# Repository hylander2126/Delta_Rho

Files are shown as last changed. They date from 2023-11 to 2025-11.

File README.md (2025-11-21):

# Delta Rho Robot
3D models, firmware, and MATLAB control scripts for the Delta-Rho swarm robotic platform at WPI's Soft Robotics Laboratory. Contact Cagdas Onal (cdonal@wpi.edu) or Steven Hyland (smhyland@wpi.edu) for more information.

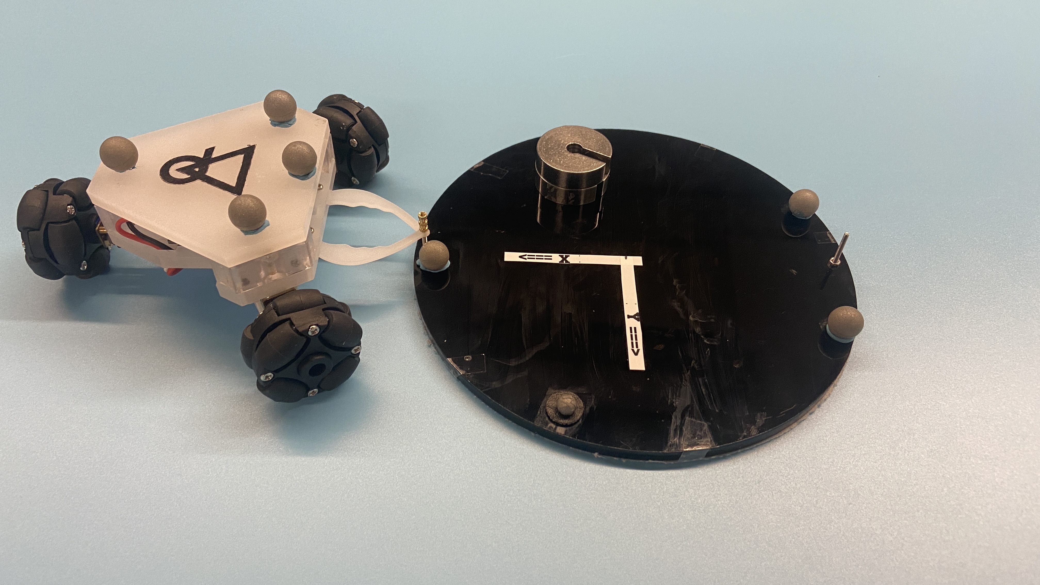
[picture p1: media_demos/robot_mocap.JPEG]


### Hardware:
#### PCB
The robot currently uses a custom PCB housing a ATMega1284p chip. More details along with a schematic can be found in the hardware/controller_board folder. It can be powered via 7.4V LiPo battery, make sure not to flip + and -

#### CAD
Currently, the robot is designed in SolidWorks, with most of the chassis and body 3D printed. Other necessary and optional components can be found in the hardware/CAD folder.

### Firmware:
Flashing firmware to the robot is performed with a standard AVRISP MKII programmer over ISP interface. Connect the programmer to the robot following following the correct wiring:
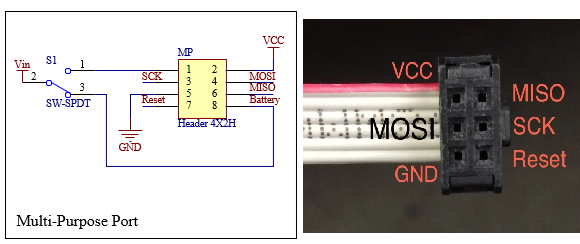
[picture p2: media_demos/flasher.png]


Use Microchip Studio and open the 'Delta_Rho_controller.atsln' solution file. Code is written in C, and can be flashed to the robot using the 'start debugging' button or pressing 'f5'. Currently, the firmware allows for onboard computation, code execution, etc. but can also be moved offboard to MATLAB (controller code provided in 'control_single_robot' folder). 

NOTE: the ROBOT ID at the top of the robot code is critical for communicating and differentiating between robots when handling a multi-robot swarm. If you are worried about interference between other robots, set these IDs to some unique integer (1 to 255). 

MATLAB Communication is performed through two Xbee RF modules, one 'server' attached to the PC via USB adapter, and one 'client' attached to the header on the robot board.  The demo script should get you started with sending velocity commands to the robot. See the 'utilities' folder for more functions.


#### Communication:
XBee modules need to be flashed to operate on the same bandwidth and to determine the 'server' and 'client' modules, respectively. This setup only needs to be performed once on new XBee modules. 

(TODO: Add programming instructions)

### Simulation:
Currently, all the simulation is performed in MATLAB. Other simulation software is in progress.

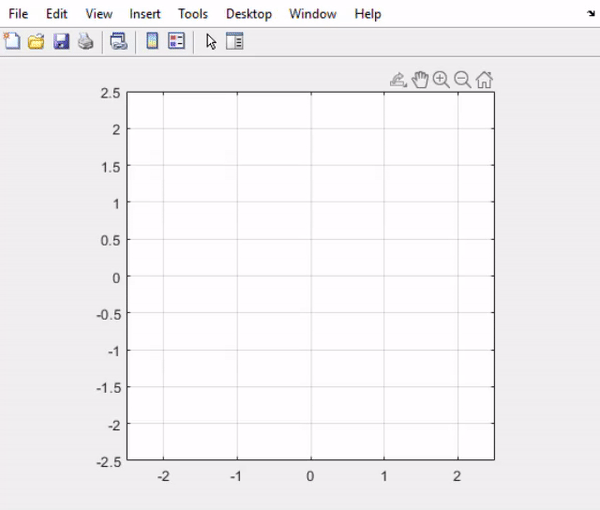
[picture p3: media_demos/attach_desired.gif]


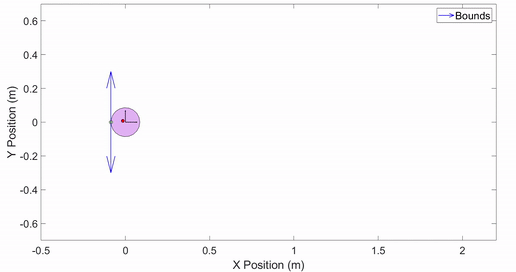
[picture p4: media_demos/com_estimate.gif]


---

Reach out to Steven Hyland at smhyland@wpi.edu for further questions or concerns.

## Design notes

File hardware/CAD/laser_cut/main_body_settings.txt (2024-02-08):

Cover spring slots with tape
2-3 raster passes at 15% speed 25% power

3 vector cuts at 15% speed 60% power

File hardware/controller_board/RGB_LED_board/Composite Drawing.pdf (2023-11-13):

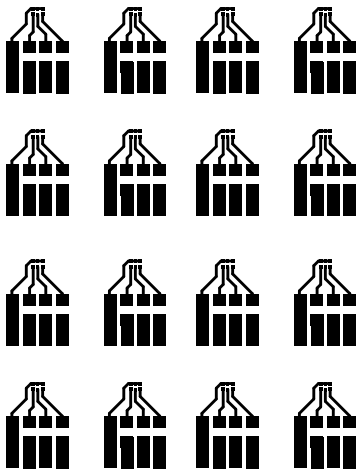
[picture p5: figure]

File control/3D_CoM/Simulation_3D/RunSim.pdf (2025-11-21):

## Full 3D Simulation of CoM Estimation Strategy

clc; clear; close all;
addpath("Utilities\");

% First set the problem and object parameters (FOR NOW A RECTANGULAR BOX)
mass | = 1;
fric | = 0.5;
width | = 2;
height = 4;
origin = [0; 0; 0]; % ORIGIN (for simplicity, this is at tipping edge on smallest y (into page) vertex)
com | = [-width/2; width/2; height/2]; % com defined from origin
hf | = 3; | % Height above the table where f applied
Pf | = [-width; 1; hf]; % point of external force applied
Fp | = [1; 0; 0]; % magnitude of linear force applied
viewf | = [0 -1 0]; % Front view (-y towards camera)
viewt | = [0 0 1]; % Top view (z towards camera)

body = body('mass',mass, 'mu',fric, 'com',com, 'width',width, ... 'height',height, 'Pf',Pf, 'Fp',Fp, 'origin',[-width;0;0]);

% Now visualize the object

% 3D view
body.plot(gca); hold off; figure;

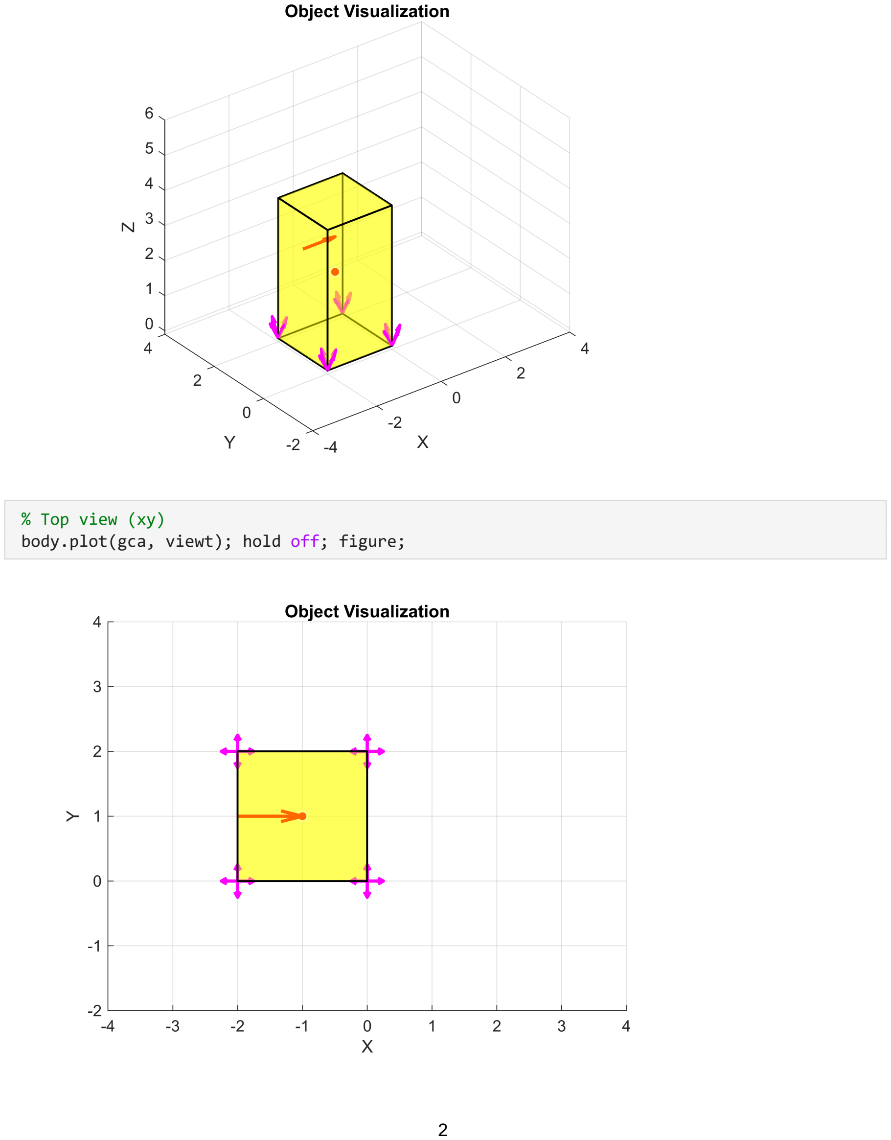
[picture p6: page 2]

% Top view (xy)
body.plot(gca, viewt); hold off; figure;

% Front view (xz)
body.plot(gca, viewf); hold off; figure;

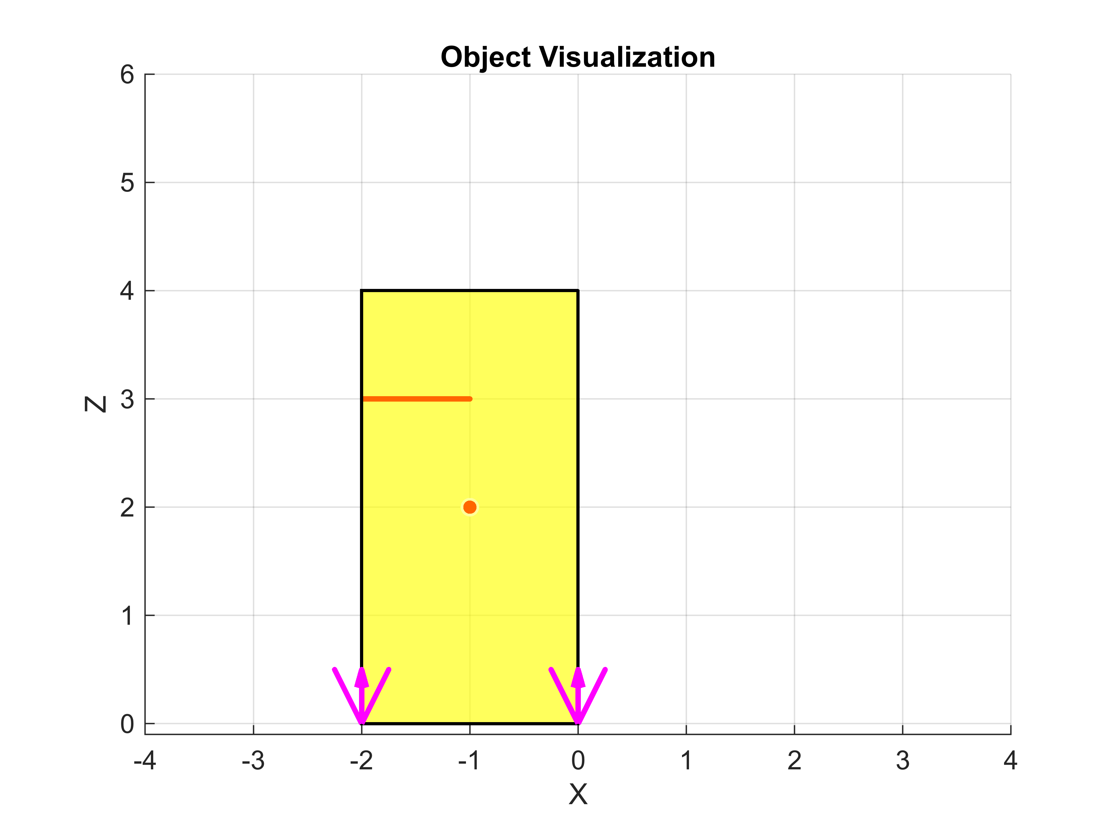
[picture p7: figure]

### First, scalar analysis of the SLIDING/TIPPING condition

% Scalar being the basic sliding/tipping thresholds

syms mu m g r_w h_c d positive
syms F_p h_f real

% Incipient SLIDING is when F(push) >= f(fric). recall that {ft <= mu*f(normal)}. x-axis equilibrium.
slide_F = solve( F_p == mu*m*g, F_p );

% Incipient TIPPING is when M(push) > M(gravity). recall that {M = f*r}. y-axis moment equilibrium.
% (also recall at incipient tip, norm and fric generate no moment since they occur @ tipping point
tip_F = solve( F_p*h_f == m*g*r_w, F_p );

% tip_cond_F = solve(subs(tip_eqn, [m g r_w h_f], [mass 9.8 -body.com(1) hf]), F_p) % r_w from com to tip edge
% should probably generalize ^this^ to check for the furthest point from the push side, but not for now slide_val = double( subs(slide_F, [mu,m,g], [fric,mass,9.8]) );
tip_val | = double( subs(tip_F, | [m,g,r_w,h_f], [mass,9.8,abs(body.com(1)),hf]) );

% Print Conditionals
cond = 'SLIDING and TIPPING';
if isAlways(slide_val < tip_val); cond = char('SLIDING'); end
if isAlways(tip_val < slide_val); cond = char('TIPPING'); end
fprintf('F required for sliding: %.3f and tipping: %.3f', slide_val, tip_val)

F required for sliding: 4.900 and tipping: 3.267
fprintf('\n%s will occur because its the smaller of the two by: %.3f.\n', cond, abs(round(slide_val - tip_val, 3)))

TIPPING will occur because its the smaller of the two by: 1.633.

% For fun, find height where sliding and tipping occurs simultaneously, given current object geometry
ts_eqn = solve(m*g*r_w/(h_f) == mu*m*g, h_f);
ts_val = double( subs(ts_eqn, [r_w mu], [-com(1) fric]) );
fprintf('h_f required for current geometry and friction: %.3f', ts_val)

h_f required for current geometry and friction: 2.000

### Next, scalar analysis of TOPPLING condition

% A finger located at Pf (relative to object frame) continually pushes with force Fp until object comes to
% unstable equilibrium (ZMP: zero moment point). At any time t during motion, static equilibrium is present

% Assume TIPPING condition is active i.e. F(t=0) = F_tip
F = tip_val;
angle_step = -0.1; % degrees. 'step' for each object/plotting update. Can be arbitrarily small.
flist = [];
topple_i = 0;

% Lets 'simulate' bringing object to toppling threshold. No physics, just visual + geometry analysis.
while F > 0
% The force required for equilibrium drops bc rw drops AND hf increases
rw_i = -body.com(1); | % x-distance from CoM to tip edge
hf_i = body.Pf(3); | % z-distance (height) of push from tip edge
% Moment equation at this time
F = (9.8*mass*rw_i)/hf_i;

topple_i = topple_i + 1;
flist = [flist; F]; % (this is the force required to maintain equilibrium at current time)

T = [R3(angle_step, [0;-1;0],'deg') [0;0;0]; 0 0 0 1];
body.move(T)
% body.plot(gca, viewf) % Uncomment to plot in the loop (CAUTION: THIS MAY CRASH MATLAB)
end

% Visualize the object and the Force graph
body.plot(gca, viewf);

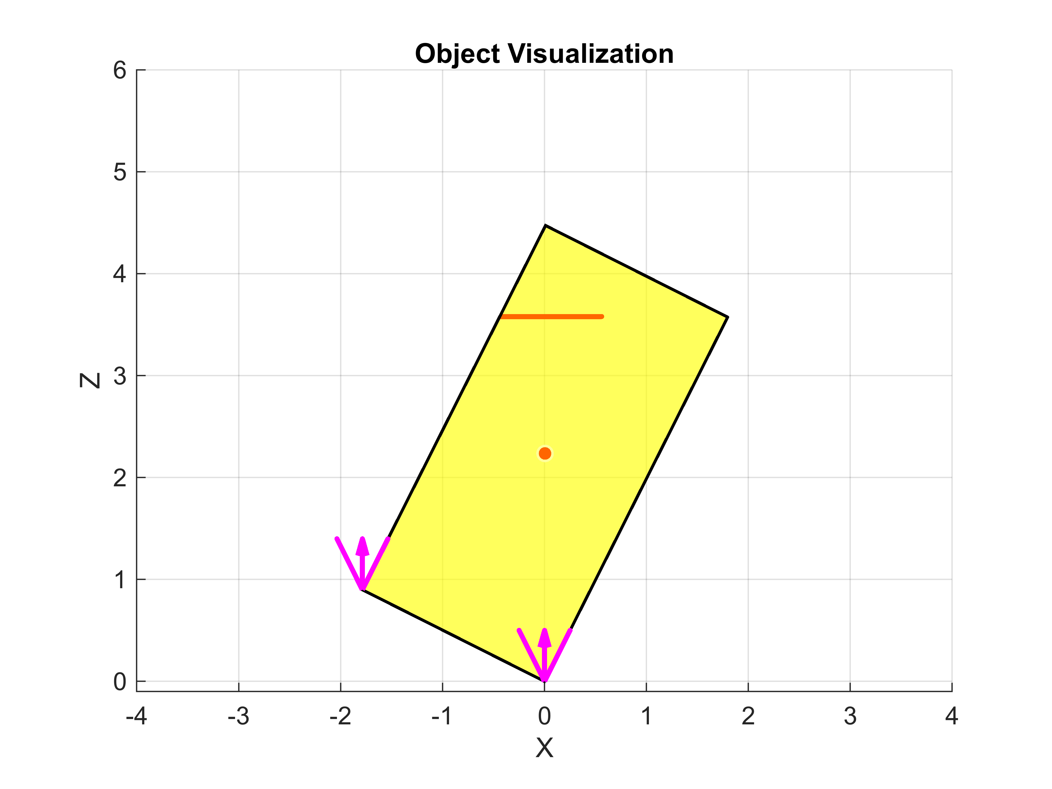
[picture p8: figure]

figure; plot(flist); hold on; xlim([0, topple_i]); ylim([-0.5 tip_val+0.5]); yline(0,'--r');
title('Force Required to Maintain Equilibrium'); hold off;

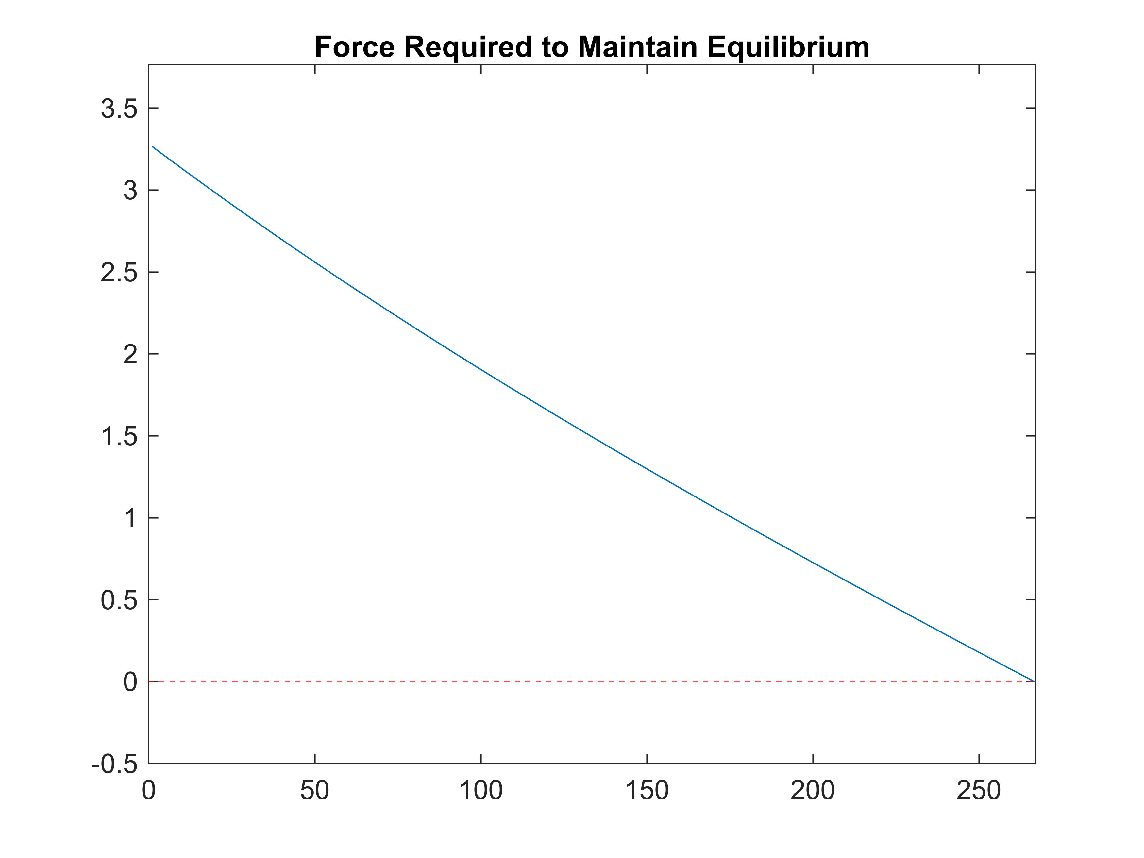
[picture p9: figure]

% Now we know the final angle of the payload at which toppling occurs. topple_final_angle = angle_step*topple_i;
fprintf('\nToppling occurs at object angle %.2f deg.', topple_final_angle)

Toppling occurs at object angle -26.70 deg.

% Let's reset the object for the next section reset_angle = -topple_final_angle;
T = [R3(reset_angle, [0;-1;0],'deg') [0;0;0]; 0 0 0 1];
body.move(T);

### Now, let's try approximating the force curve with a small push

angle_step = -0.1; % again, arbitrary. akin to time step.
final_angle = -5; % degrees. 'final' angle - bring object to this angle and no further
topple_angles = [];
flist_approx = [];

start_angle = 0;

for j = 0 : angle_step : final_angle
% The force required for equilibrium drops because rw drops AND hf increases

rw_i = -(body.com(1));
hf_i = body.Pf(3);
% Moment equation at this time
F_approx = (9.8*mass*rw_i)/hf_i;

topple_angles = [topple_angles; j];
flist_approx = [flist_approx; F_approx]; % (this is the force required to maintain equilibrium at current time)

T = [R3(j - start_angle, [0;-1;0],'deg') [0;0;0]; 0 0 0 1];
body.move(T);
% body.plot(gca, viewf) % Uncomment to plot in the loop (CAUTION: THIS MAY CRASH MATLAB)
start_angle = j;
end

% For visualization, make topple angles positive topple_angles_mag = abs(topple_angles);

% Visualize the object and the Force graph close all;
body.plot(gca, viewf); hold off;

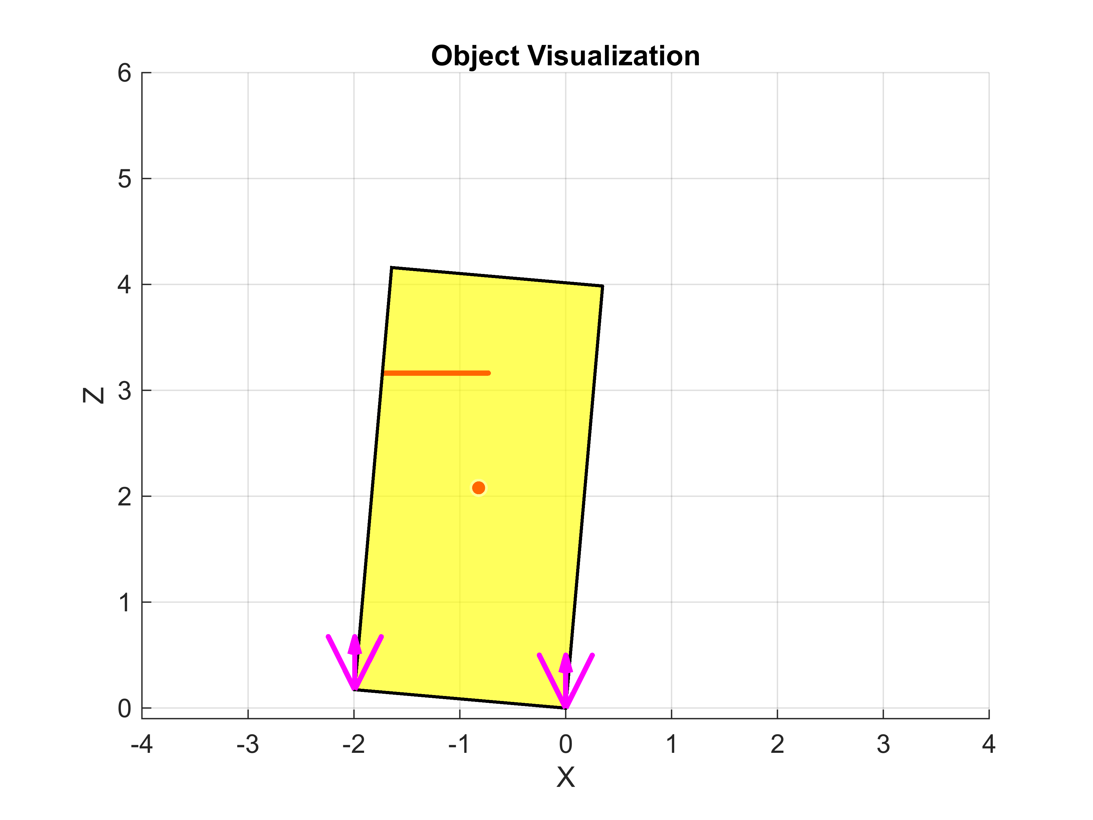
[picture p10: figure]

figure; plot(topple_angles_mag, flist_approx); yline(0,'--r'); title('Force Required to Maintain Equilibrium'); hold on;

% Now let's approximate the force curve given the data subset
n = 1; % use 5th order for decent approximation
p = polyfit(topple_angles_mag, flist_approx, n); % Fit a polynomial approximation r = roots(p);
topple_angle_approx = r( imag(r)==0 ); % Save only the real roots

% Visualize the approximation
xx = linspace(abs(final_angle), topple_angle_approx, 20);
yy = polyval(p, xx);
plot(xx, yy, 'k-.'); xlim([0, topple_angle_approx]); ylim([-0.5 tip_val+0.5]);

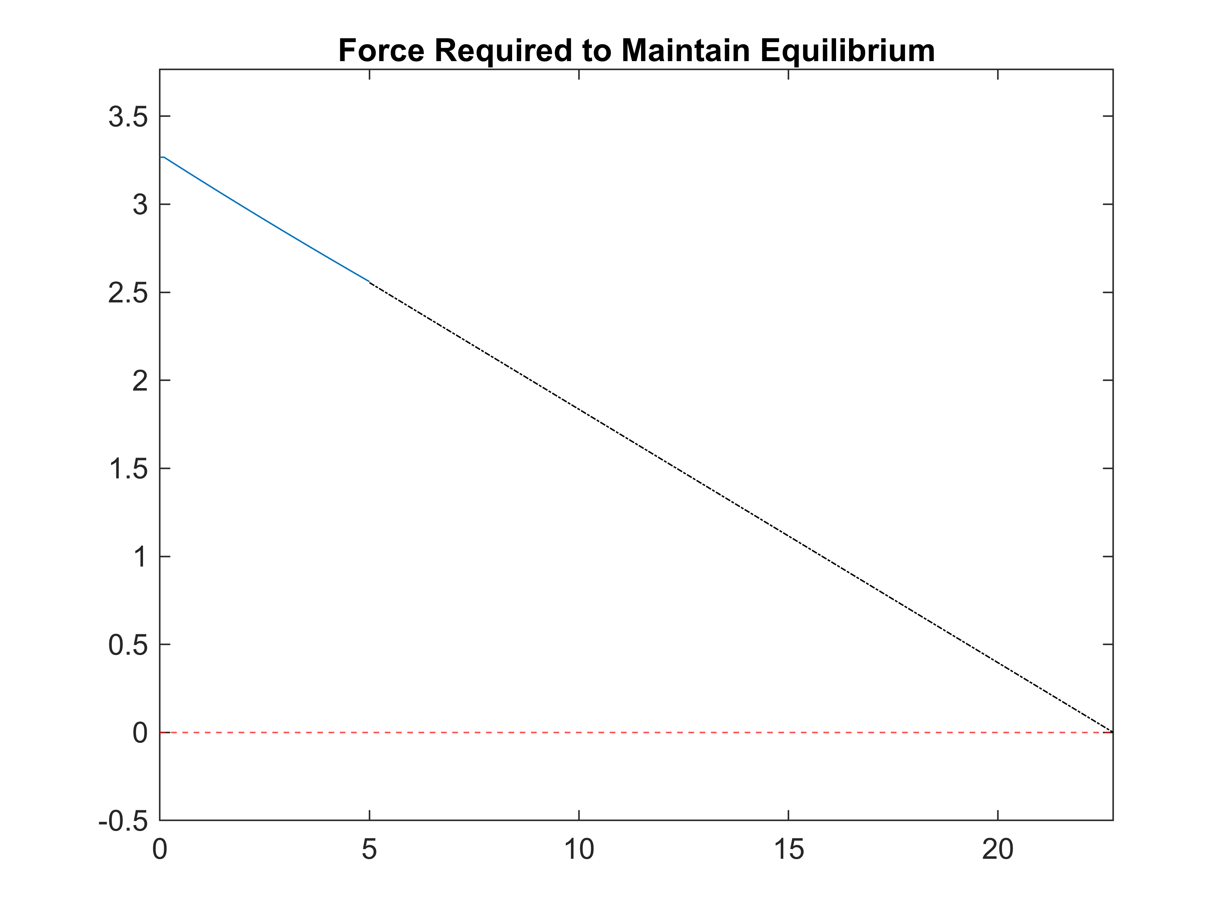
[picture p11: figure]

% Now we know APPROXIMATELY angle at which toppling occurs. fprintf(['\nToppling occurs at approximately %.2f deg. We know the CoM is\n' ... 'on the plane that is this angle from the plane of travel.'], sign(final_angle)*topple_angle_approx)

Toppling occurs at approximately -22.75 deg. We know the CoM is
on the plane that is this angle from the plane of travel.

% Let's reset the object for the next section reset_angle = -topple_angles(end);
T = [R3(reset_angle, [0;-1;0],'deg') [0;0;0]; 0 0 0 1]; body.move(T);

% Finally, let's try to calculate the CoM possibilities using this:

% Use the approximate tipping angle you found:
theta_app = sign(final_angle) * topple_angle_approx; | % in degrees
theta_rad = deg2rad(theta_app); | % convert to radians

% Solve for z_c in terms of x_c on the tipping plane:
syms xc zc real
% zc_plane = solve( xc*cos(theta_rad) + zc*sin(theta_rad) == 0, zc ); zc_plane = solve( zc == xc/tan(theta_rad), zc );

% Sample across the object width:
xc_vals = linspace(-width/2, width/2, 50); | % plausible x_c range
yc_vals = zeros([1, length(xc_vals)]); | % y_c = 0
zc_vals = double( subs(zc_plane, xc, xc_vals) ); | % corresponding z_c

figure;
body.plot(gca, viewf);
hold on;
% Plot the result
poss_com_vals = plot3(xc_vals, yc_vals, zc_vals, 'b-', 'LineWidth', 2); % also mark your current COM for reference
xlabel('x_c (m)');
ylabel('z_c (m)');
title(sprintf('Possible COM locations @ tipping angle ≈ %.2f°', theta_app)); legend(poss_com_vals,'Tipping-plane','Location','best');
grid on;

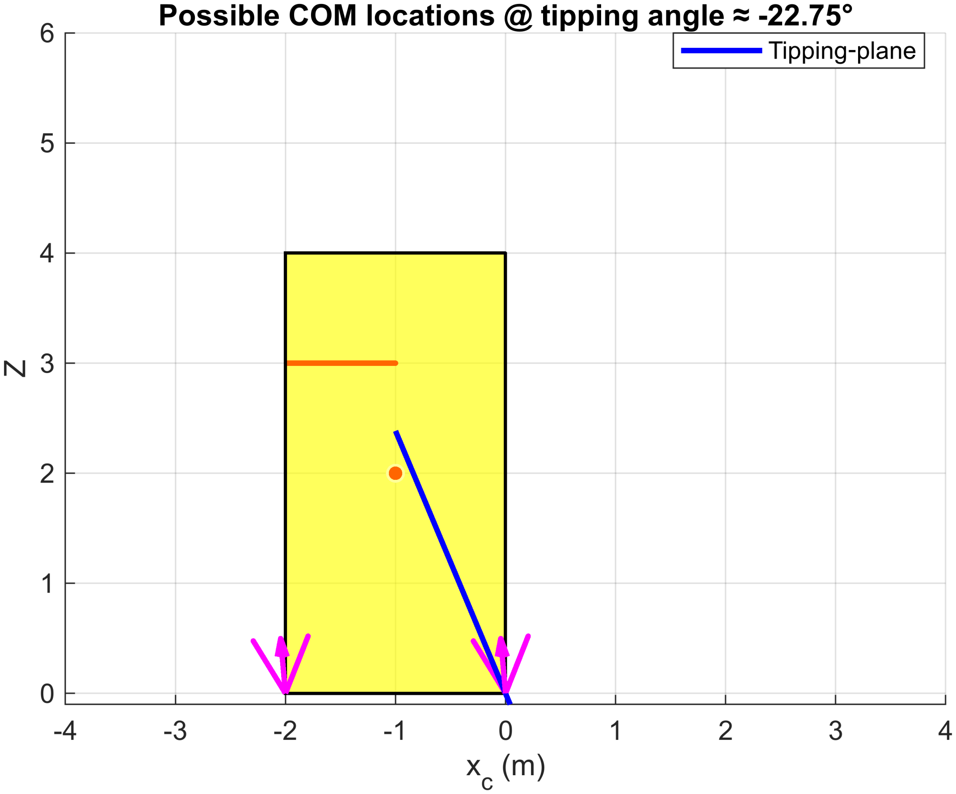
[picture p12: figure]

### Given this, we can now either:

1. Use our 2D CoM to approximate the 3D CoM
2. Push from a different side to get two planes, then find their intersection

Possible (complete!) Procedure:

1. Analyze object to determine optimal pushing side opposite flat edge, if possible.
2. Trial a push somewhere along its height, start in the middle.
3. If not tipping, move upwards until beyond/above tipping threshold.
4. Now push for a bit towards toppling point and collect F/T data
5. Calculate plane that vertical CoM lies within.
6. Perform option 1 or 2 from above to get 3D CoM.

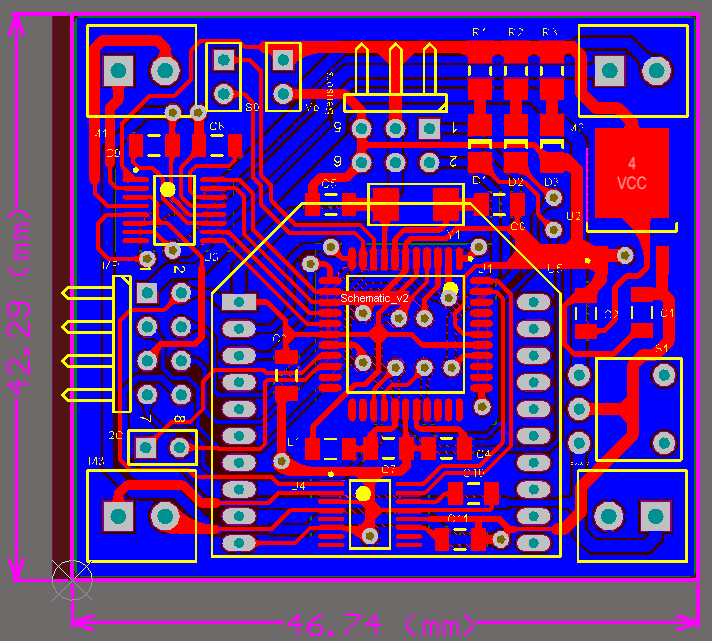
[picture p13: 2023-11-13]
hardware/controller_board/v2/PCB.PNG

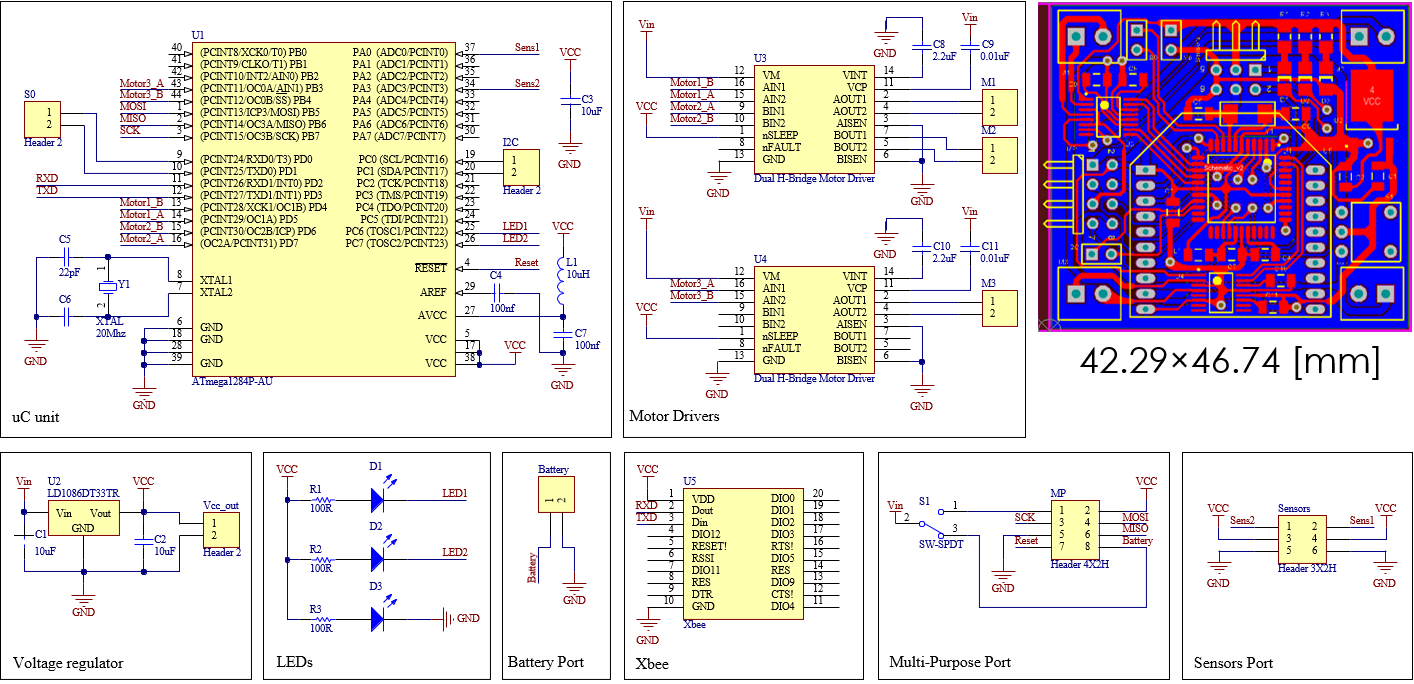
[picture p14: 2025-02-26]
hardware/board1.png

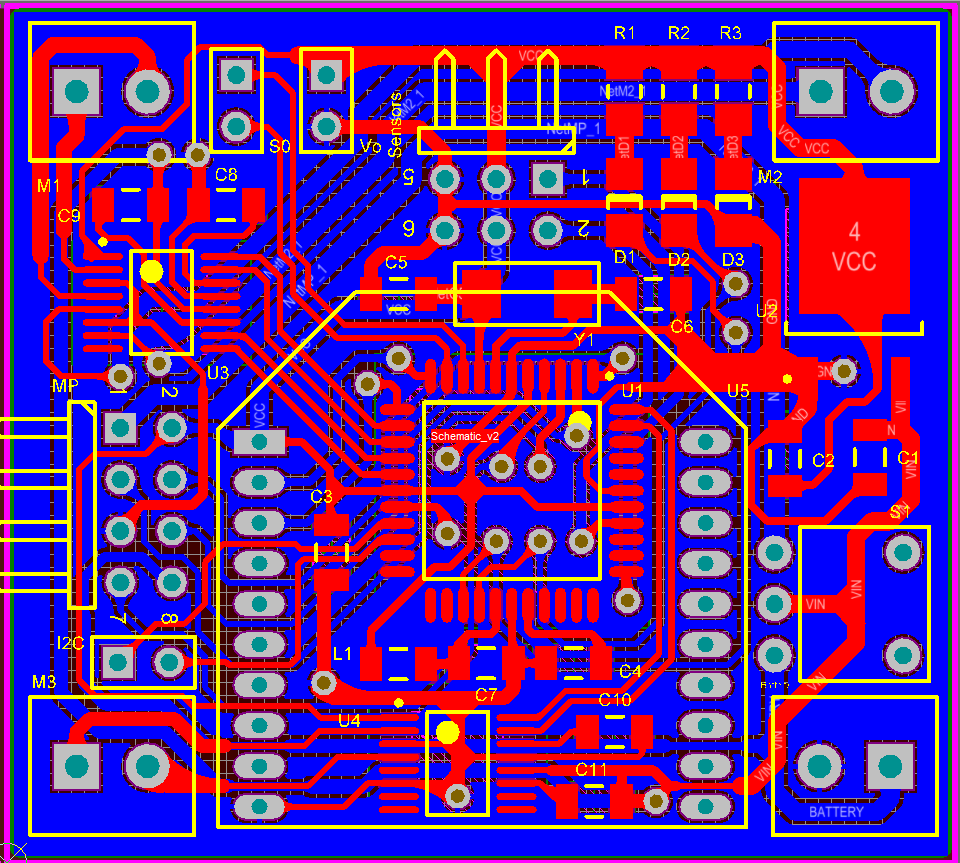
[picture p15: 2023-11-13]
hardware/controller_board/v2/board.PNG

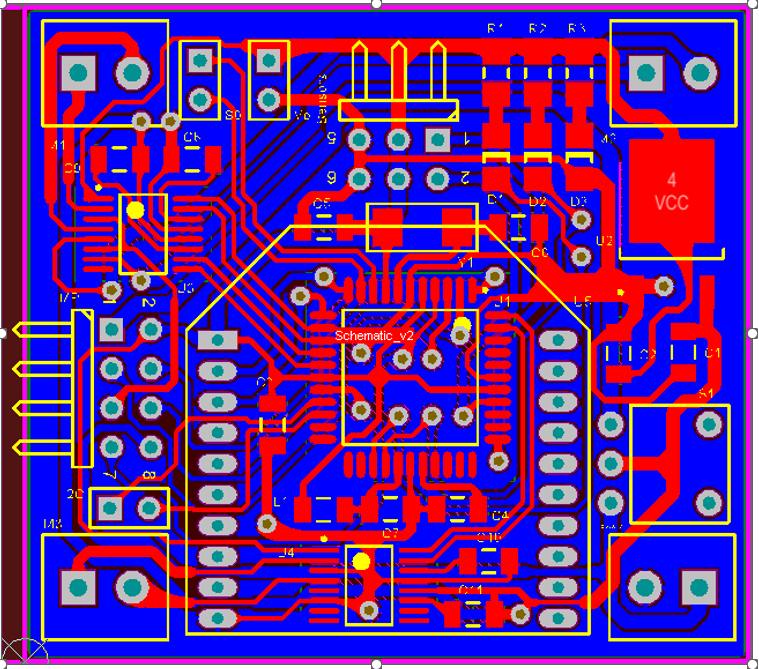
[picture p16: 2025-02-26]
hardware/controller_board/board2.png

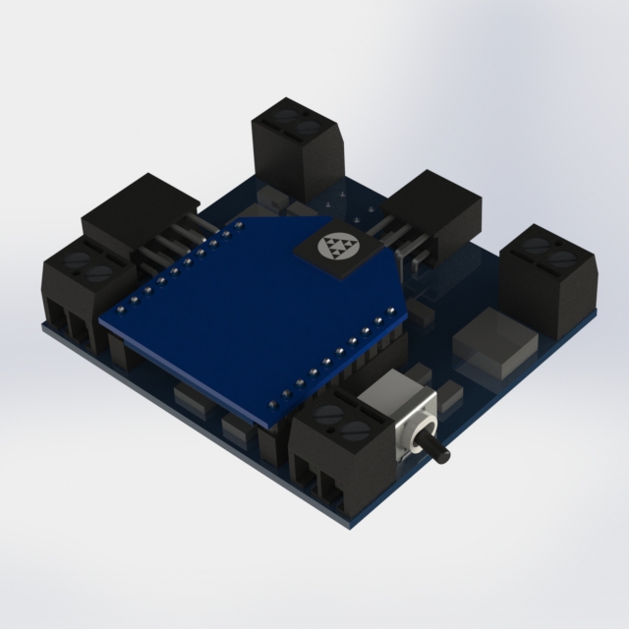
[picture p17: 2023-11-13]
hardware/controller_board/v2/Circuit.JPG

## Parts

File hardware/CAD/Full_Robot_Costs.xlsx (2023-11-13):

Part | Quantity | Unit Price | Total Cost | Link
Omni Wheels | 3 | $4.00 | $12.00
Motors | 3 | $6.32 | $18.96
Motor Brackets | 3 | $2.71 | $8.13
Battery | 1 | $4.99 | $4.99
Raspberry Pi Pico | 1 | $6.00 | $6.00
Motor Driver | 1 | $15.00 | $15.00
3D-Printed Parts | 1 | $0.70 | $0.70
 |  | Grand Total | $65.78

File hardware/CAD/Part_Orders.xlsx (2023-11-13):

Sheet: Sheet1
 | Date | Supplier | Part No. | Part Name | Quantity | Unit Price | Total Price | Shipping? | Link
 | 2023-03-23 | Ozrobotics | 14184 | 38mm Double Plastic Omni Whel w/ 8 PU Rollers | 12 | 4 | 48 | 27 | https://ozrobotics.com/shop/38mm-1-5-inches-double-plastic-omni-wheel-with-8-pu-rollers-the-smallest-omni-wheel-14184/
 | 2023-03-23 | Pimoroni | COM0818 | Micro Metal Gearmotor (Extended back shaft) 110:1 | 15 | 6.27 | 94.05 | 12.3 | https://shop.pimoroni.com/products/micro-metal-gearmotor-extended-back-shaft?variant=32587851338
 | 2023-03-23 | Pololu | 989 | Micro Metal Gearmotor Bracket Pair | 8 | 2.71 | 21.68 |  | https://www.pololu.com/product/989
 | 2023-03-23 | Pololu | 2135 | DRV8835 Dual Motor Driver Carrier | 1 | 9.95 | 9.95 |  | https://www.pololu.com/product/2135
 | 2023-03-23 | Adafruit | 259 | USB LiIon/LiPoly Charger - v1.2 | 1 | 12.5 | 12.5 |  | https://www.adafruit.com/product/259
 | 2023-03-23 | Adafruit | 5526 | Raspberry Pi Pico W | 2 | 6.00 | 12 |  | https://www.adafruit.com/product/5526
 | 2023-03-23 | Waveshare | 19764 | DC Motor Driver Module for Rpi Pico, 4x | 1 | 14.99 | 14.99 |  | https://www.waveshare.com/pico-motor-driver.htm
Lab Supp | 2023-03-23 | Amazon | ‎BH-SW6308450 | 2-in-1 Solder Wire and Rosin Paste Flux Kit: 1Lb Tin Lead Rosin Core Solder Wire (0.8mm 450g) and 1 Jar Soldering Flux | 1 | 29.99 | 29.99 |  | https://a.co/d/adxnUnD
Lab Supp | 2023-03-23 | Amazon | B07PKKY8BX | MCIGICM 10pcs Male Header Pin, 40 Pin Header Strip | 1 | 4.99 | 4.99 |  | https://a.co/d/cievj7X
 | IDK | Turnigy | 9067000511-0 | Nano-tech 260mAh 2S 35-70C Lipo Battery | 6? | 4.99 | 29.94 |  | https://hobbyking.com/en_us/turnigy-nano-tech-260mah-2s-35-70c-lipo-battery.html
 | 2023-06-02 | Bourns | 3382H-1-103 | 3382H-1-103 Resistive Rotary Position Hole for Shaft PC Pin | 16 | 2.27 | 36.256 |  | https://www.digikey.com/en/products/detail/bourns-inc/3382H-1-103/2080233
 | 2023-06-02 | Waveshare | 19764 | DC Motor Driver Module for Rpi Pico, 4x | 1 | 14.99 | 14.99 |  | https://www.waveshare.com/pico-motor-driver.htm
 |  |  |  |  |  |  | 329.336

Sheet: Single Robot Materials
Single Robot Required Materials
 | Supplier | Part No. | Part Name | Quantity | Unit Price | Total Price | Link
 | Ozrobotics | 14184 | 38mm Double Plastic Omni Whel w/ 8 PU Rollers | 3 | 4 | 12 | https://ozrobotics.com/shop/38mm-1-5-inches-double-plastic-omni-wheel-with-8-pu-rollers-the-smallest-omni-wheel-14184/
 | Pololu |  | Micro Metal Gear Motor | 3
 | Pololu | 989 | Micro Metal Gearmotor Bracket Pair | 2 | 2.71 | 5.42 | https://www.pololu.com/product/989
 | HobbyKing | 9067000511-0 | Turnigy 260mah 2S 35~75C Lipo Battery | 1 | 4.99 | 4.99 | https://hobbyking.com/en_us/turnigy-nano-tech-260mah-2s-35-70c-lipo-battery.html
 | Adafruit | 259 | USB LiIon/LiPoly Charger - v1.2 | 1 | 12.5 | 12.5 | https://www.adafruit.com/product/259
 | Waveshare | 11293 | Xbee USB Adapter | 1 | 6.99 | 6.99 | https://www.waveshare.com/xbee-usb-adapter.htm
 | Fasteners:
 |  | 99461A914 | Philips Thread-forming screws m2x5mm | 4 | 7.04 | 28.16 | https://www.mcmaster.com/99461A914/

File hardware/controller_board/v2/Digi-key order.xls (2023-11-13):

PURCHASE ORDER REQUEST FORM
Mechanical Engineering Department | This form must be filled out completely
 | see attached sample
Company Information: | Requested by:
Co. Name: Digi key | Name: Shadi Tasdighi Kalat
Street Address: 701 Brooks Avenue South, | Email Address: stasdighikalat@wpi.edu
City, State: Thief River Falls, MN 56701
 | MQP Name:
Contact Person: | (if applicable)
(If you speak to someone at co.)
Phone #218-681-6674 | Account to Charge:
Fax #: 218-681-3380 | (Professor will provide this)
 |  |  | Unit | Total
Model or Part # | Item Description: | Qty: | Price: | Price:
587-1346-1-ND (http://www.digikey.com/product-search/en?vendor=0&keywords=587-1346-1-ND) | 10 µF Capacitor | 20 | 0.232 | 4.64
709-1302-1-ND (http://www.digikey.com/product-detail/en/202R18N220KV4E/709-1302-1-ND/2237059) | 22 pF Capacitor | 15 | 0.29 | 4.35
490-1767-1-ND (http://www.digikey.com/product-detail/en/GRM31C5C1E104JA01L/490-1767-1-ND/587366) | 100 nF Capacitor | 15 | 0.276 | 4.14
490-4796-1-ND (http://www.digikey.com/product-detail/en/GCM31CR71H225KA55L/490-4796-1-ND/1641715) | 2.2µF Capacitor | 15 | 0.426 | 6.39
490-1754-1-ND (http://www.digikey.com/product-detail/en/GRM3195C1H103JA01D/490-1754-1-ND/587595) | 0.01µF Capacitor | 15 | 0.356 | 5.34
A105685-ND (http://www.digikey.com/product-detail/en/8-1879255-5/A105685-ND/2376209) | 100R Resistor | 20 | 0.85 | 17
887-1248-ND (http://www.digikey.com/product-detail/en/9B-20.000MEEJ-B/887-1248-ND/2207668) | 20 MHz Crystal | 7 | 0.48 | 3.36
535-11657-1-ND (http://www.digikey.com/product-detail/en/AIML-1206-100K-T/535-11657-1-ND/2782918) | 10 µH Inductor | 20 | 0.195 | 3.9
160-1405-1-ND (http://www.digikey.com/product-detail/en/LTST-C150KRKT/160-1405-1-ND/386760) | Red LED | 10 | 0.288 | 2.88
160-1643-1-ND (http://www.digikey.com/product-detail/en/LTST-C150TBKT/160-1643-1-ND/573584) | Blue LED | 10 | 0.371 | 3.71
160-1456-1-ND (http://www.digikey.com/product-detail/en/LTST-C230KGKT/160-1456-1-ND/386854) | Green LED | 10 | 0.287 | 2.87
ED2740-ND (http://www.digikey.com/product-detail/en/OSTTE020104/ED2740-ND/2351816) | Terminal Block - Wire to board | 25 | 0.312 | 7.8
S5517-ND (http://www.digikey.com/product-detail/en/PPTC032LJBN-RC/S5517-ND/775975) | Header 3x2H | 10 | 0.878 | 8.78
609-3353-ND (http://www.digikey.com/product-detail/en/68021-408HLF/609-3353-ND/1878524) | Header 4x2H | 10 | 0.428 | 4.28
497-3446-1-ND (http://www.digikey.com/product-detail/en/LD1086DT33TR/497-3446-1-ND/669240) | 3.3 Volt regulator | 10 | 0.784 | 7.84
296-40080-1-ND (http://www.digikey.com/product-detail/en/DRV8833PWR/296-40080-1-ND/5177957) | Dual H-Bridge motor driver | 15 | 2.074 | 31.11
ATMEGA1284P-AU-ND (http://www.digikey.com/product-detail/en/ATMEGA1284P-AU/ATMEGA1284P-AU-ND/1914519) | ATmega1284p-AU Microcontroller | 7 | 8.4 | 58.8
602-1273-ND (http://www.digikey.com/product-detail/en/XB24-API-001/602-1273-ND/3482588) | RF Transceiver X-bee | 5 | 19.00 | 95
CKN1780-ND (http://www.digikey.com/product-search/en?vendor=0&keywords=GT11MABE) | on-off-on Switch | 7 | 4.71 | 32.97
S5751-10-ND (http://www.digikey.com/product-detail/en/NPPN101BFCN-RC/S5751-10-ND/804812) | X-bee header | 25 | 0.9424 | 23.56
Total: |  |  |  | 328.72
Faculty Advisor Signature:

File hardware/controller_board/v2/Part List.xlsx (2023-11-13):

Holonomic Robot Controller board
Number of boards | 5
Name | Value | Manufacturer Part Number | Digi-Key Part Number | Package | Link | Quantity [per board] | SF | Quantity [Total]
c1, c2, c3 | 10 µF | 587-1346-1-ND | 587-1346-1-ND | 1206 | http://www.digikey.com/product-search/en?vendor=0&keywords=587-1346-1-ND | 3 |  | 15
c5, c6 | 22 pF | 202R18N220KV4E | 709-1302-1-ND (http://www.digikey.com/product-detail/en/202R18N220KV4E/709-1302-1-ND/2237059) | 1206 | http://www.digikey.com/product-detail/en/202R18N220KV4E/709-1302-1-ND/2237059 | 2 |  | 10
c4, c7 | 100 nF | GRM31C5C1E104JA01L | 490-1767-1-ND | 1206 | http://www.digikey.com/product-detail/en/GRM31C5C1E104JA01L/490-1767-1-ND/587366 | 2 |  | 10
c8, c10 | 2.2µF | GRM31C5C1E104JA01L | 490-4796-1-ND | 1206 | http://www.digikey.com/product-detail/en/GCM31CR71H225KA55L/490-4796-1-ND/1641715 | 2 |  | 10
c9, c11 | 0.01µF | GRM3195C1H103JA01D | 490-1754-1-ND | 1206 | http://www.digikey.com/product-detail/en/GRM3195C1H103JA01D/490-1754-1-ND/587595 | 2 |  | 10
R1, R2, R3 | 100R Resistor | 8-1879255-5 | A105685-ND | 1206 | http://www.digikey.com/product-detail/en/8-1879255-5/A105685-ND/2376209 | 3 |  | 15
Y1 | 20 MHz | 9B-20.000MEEJ-B | 887-1248-ND | DIP | http://www.digikey.com/product-detail/en/9B-20.000MEEJ-B/887-1248-ND/2207668 | 1 |  | 5
L1 | 10 µH inductor | AIML-1206-100K-T | 535-11657-1-ND | 1206 | http://www.digikey.com/product-detail/en/AIML-1206-100K-T/535-11657-1-ND/2782918 | 3 |  | 15
D1 | Red | LTST-C150KRKT | 160-1405-1-ND | 1206 | http://www.digikey.com/product-detail/en/LTST-C150KRKT/160-1405-1-ND/386760 | 1 |  | 5
D2 | Blue | LTST-C150TBKT | 160-1643-1-ND | 1206 | http://www.digikey.com/product-detail/en/LTST-C150TBKT/160-1643-1-ND/573584 | 1 |  | 5
D3 | Green | LTST-C230KGKT | 160-1456-1-ND | 1206 | http://www.digikey.com/product-detail/en/LTST-C230KGKT/160-1456-1-ND/386854 | 1 |  | 5
Battery, M1, M2, M3 | Terminal Block - Wire to board | OSTTE020104 | ED2740-ND | DIP | http://www.digikey.com/product-detail/en/OSTTE020104/ED2740-ND/2351816 | 4 |  | 20
sensors | Header 3x2H (female) | PPTC032LJBN-RC (Pitch = 0.100" [2.54 mm]) | S5517-ND | DIP | http://www.digikey.com/product-detail/en/PPTC032LJBN-RC/S5517-ND/775975 | 1 |  | 5
MP | Header 4x2H (female) | PPTC042LJBN-RC (Pitch = 0.100" [2.54 mm]) | S5518-ND | DIP | http://www.digikey.com/product-search/en?vendor=0&keywords=PPTC042LJBN-RC | 1 |  | 5
U2 | 3.3 Volt regulator | LD1086DT33TR | 497-3446-1-ND | SMD | http://www.digikey.com/product-detail/en/LD1086DT33TR/497-3446-1-ND/669240 | 1 |  | 5
U3, U4 | Dual H-Bridge motor driver | DRV8833 | 296-40080-1-ND | SMD | http://www.digikey.com/product-detail/en/DRV8833PWR/296-40080-1-ND/5177957 | 2 |  | 10
U1 | Microcontroller | ATmega1284P-AU | ATMEGA1284P-AU-ND | SMD | http://www.digikey.com/product-detail/en/ATMEGA1284P-AU/ATMEGA1284P-AU-ND/1914519 | 1 |  | 5
Xbee | RF Transceiver | Xbee series 1 - 805.11 | 602-1273-ND | DIP | http://www.digikey.com/product-detail/en/XB24-API-001/602-1273-ND/3482588 | 1 |  | 5
S1 | on-off-on Switch | GT11MABE | CKN1780-ND | DIP | http://www.digikey.com/product-search/en?vendor=0&keywords=GT11MABE | 1 |  | 5
Xbee headers | Female header | NPPN101BFCN-RC (Picth = 0.079" [2.00 mm]) | S5751-10-ND | DIP | http://www.digikey.com/product-detail/en/NPPN101BFCN-RC/S5751-10-ND/804812 | 2 |  | 10

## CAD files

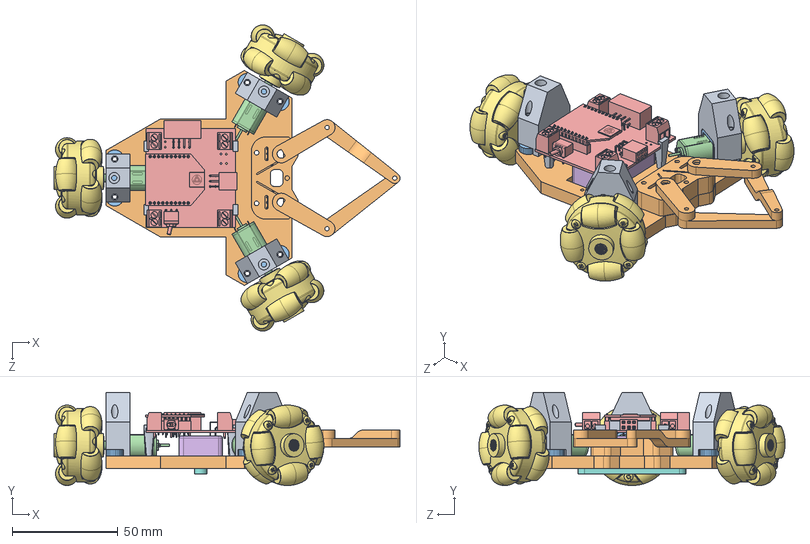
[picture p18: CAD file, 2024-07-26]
hardware/CAD/assem_full_robot_v4.SLDASM
163.8 x 44.0 x 145.0 mm
DR_body_v5
DFRobot_Micro_Metal_Bracket x 3
micro-metal-gearmotor-backshaft x 3
PCB
260mAh_battery
omni_wheel x 3
DR_battery_housing_v5
PCB_spacer x 4
5bar
DR_layer_spacer_v2 x 3

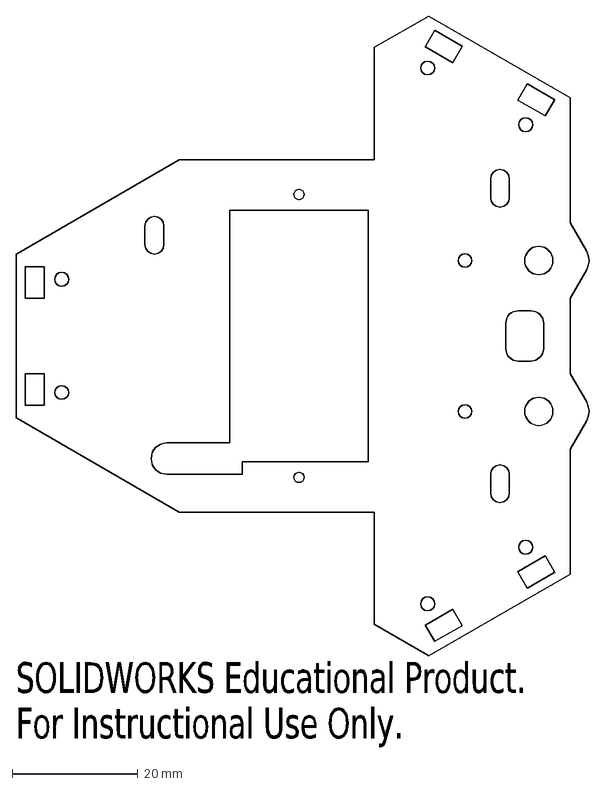
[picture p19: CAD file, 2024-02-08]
hardware/CAD/laser_cut/main_body_v4.DXF
SOLIDWORKS Educational Product.
For Instructional Use Only.

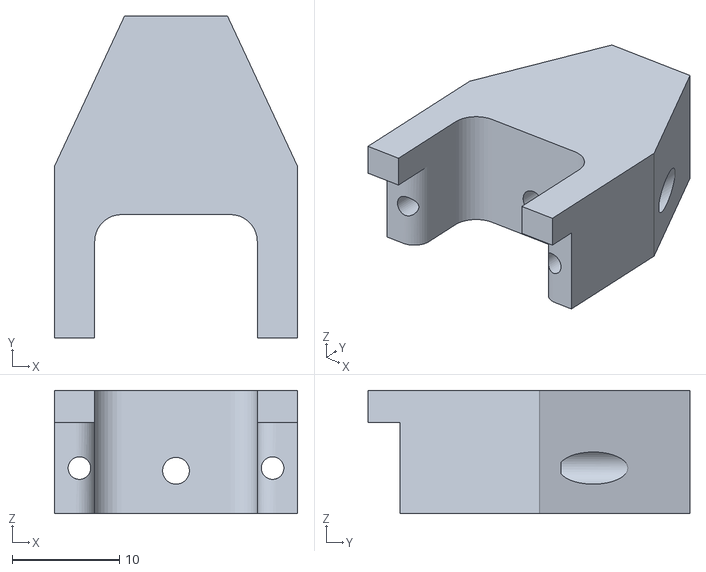
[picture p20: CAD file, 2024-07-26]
hardware/CAD/3d_print/layer_spacer_v2.STL
22.6 x 30.0 x 11.5

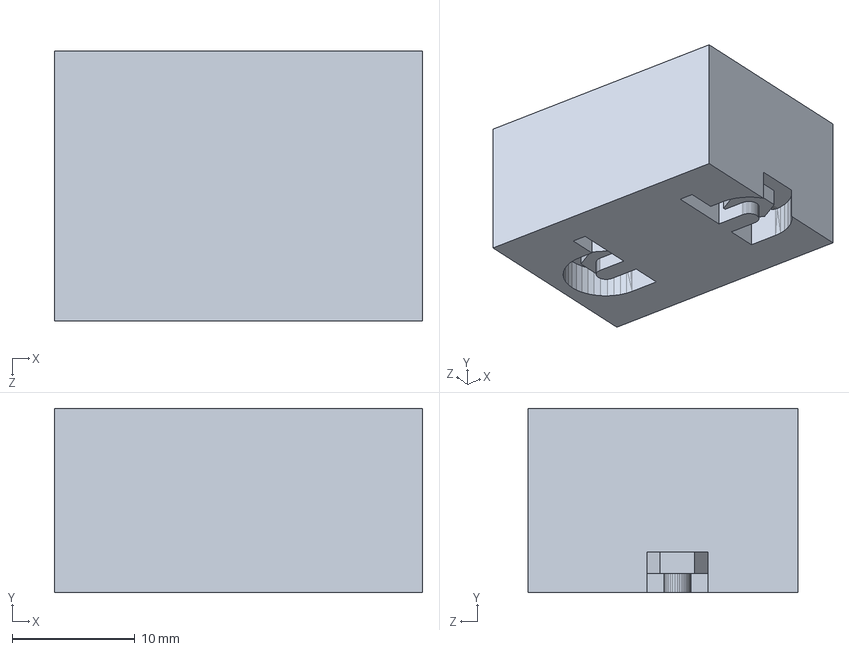
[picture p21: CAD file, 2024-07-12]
hardware/CAD/part_models/lid_spacer.SLDPRT
30.0 x 15.0 x 22.0 mm

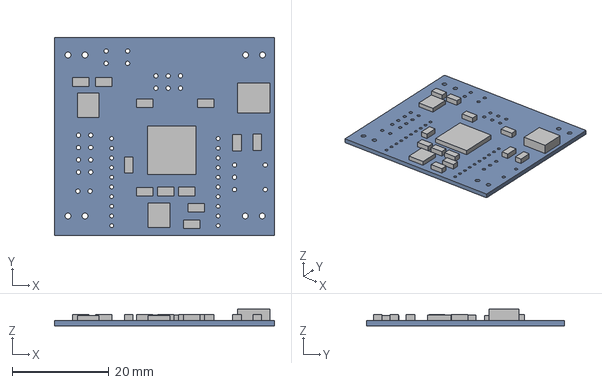
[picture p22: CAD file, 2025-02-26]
hardware/controller_board/v2/PCB.step
45.5 x 40.9 x 3.48 mm
Board
Extruded x 16

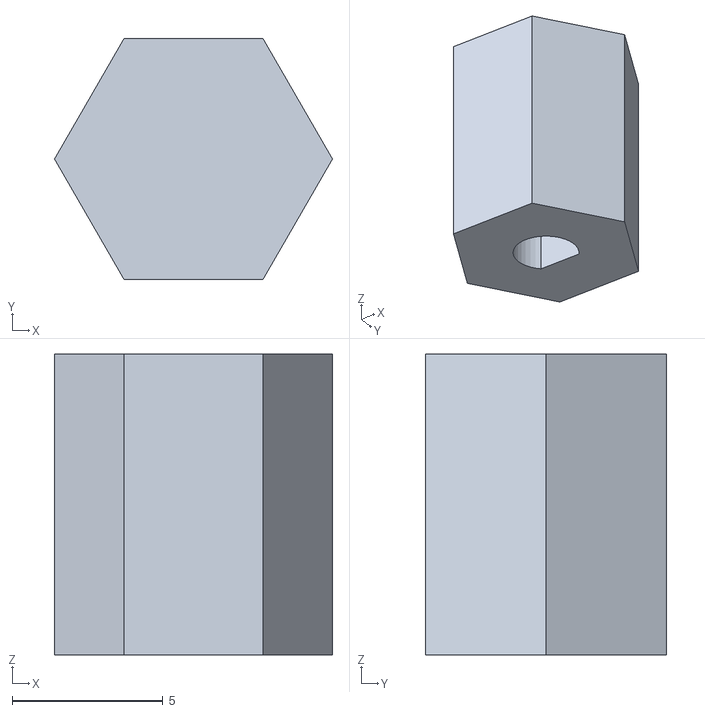
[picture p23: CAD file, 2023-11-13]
hardware/CAD/3d_print/New_Omniwheel_Coupler.STL
9.24 x 8.00 x 10.0

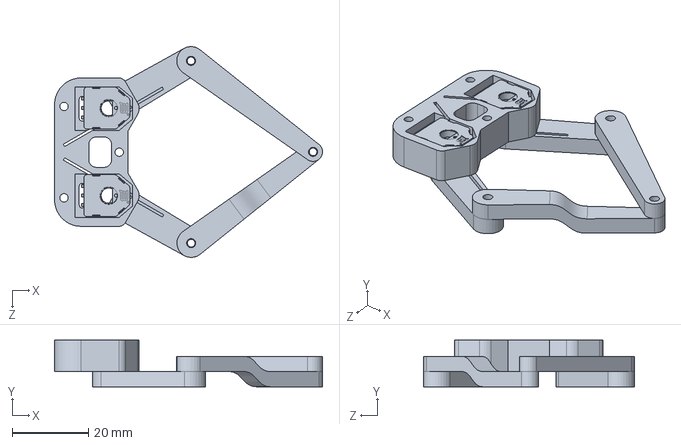
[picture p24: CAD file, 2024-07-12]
hardware/CAD/part_models/5bar.SLDPRT
70.4 x 12.2 x 55.4 mm

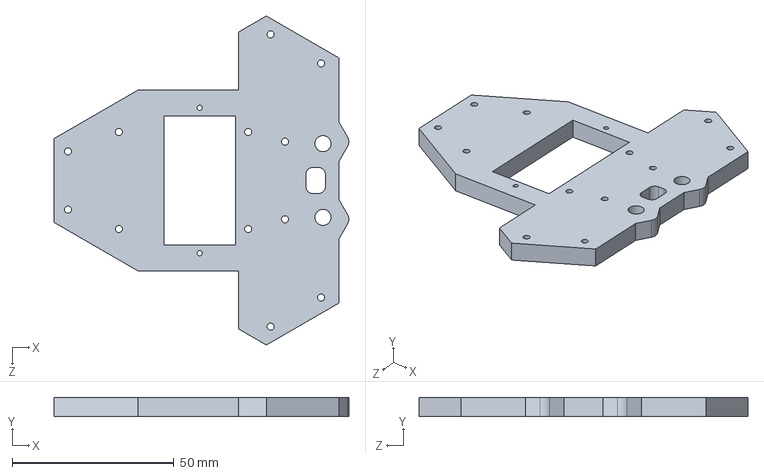
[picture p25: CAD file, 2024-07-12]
hardware/CAD/DR_body_v5.SLDPRT
91.1 x 6.00 x 101.8 mm

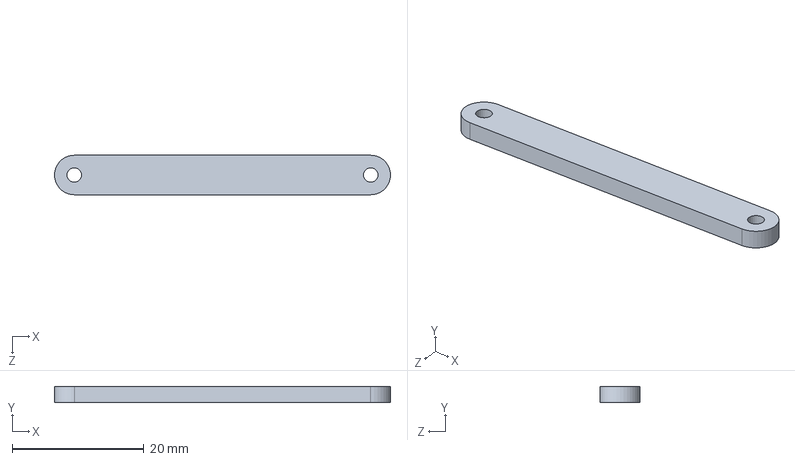
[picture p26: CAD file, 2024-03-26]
hardware/CAD/DR_battery_housing_v5.SLDPRT
51.0 x 2.50 x 6.00 mm

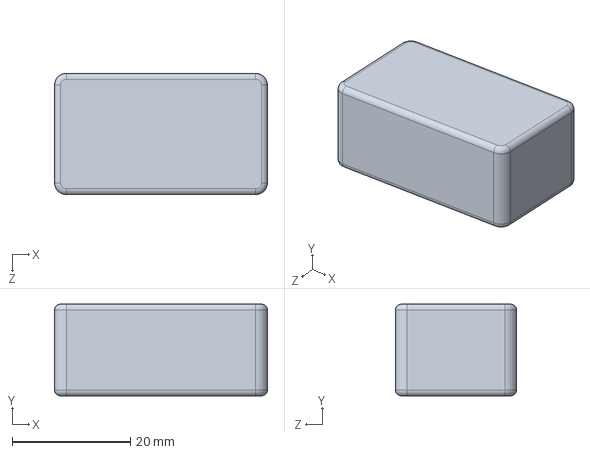
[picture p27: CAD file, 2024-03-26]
hardware/CAD/part_models/260mAh_battery.SLDPRT
36.0 x 15.5 x 20.5 mm

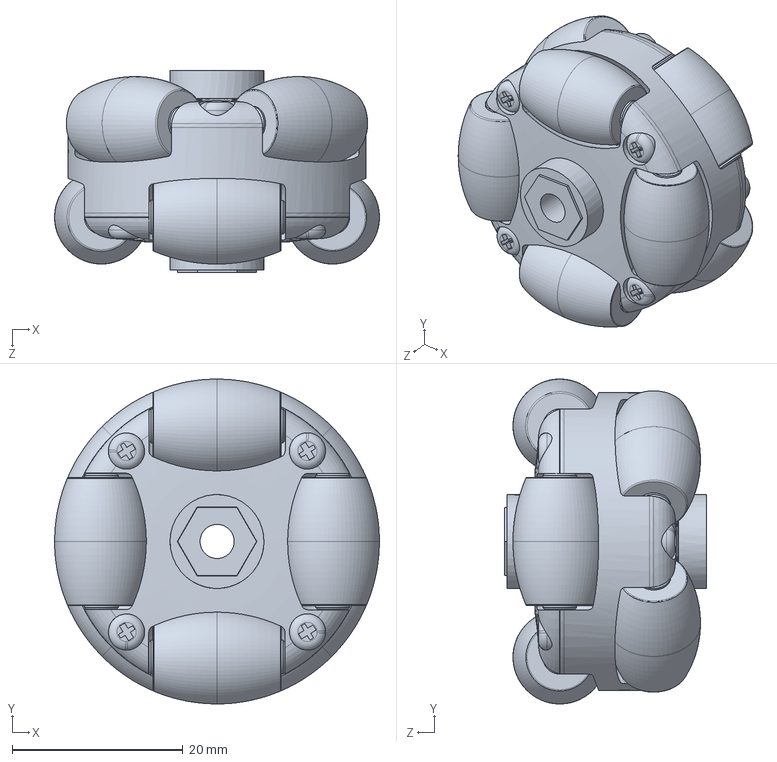
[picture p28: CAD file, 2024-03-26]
hardware/CAD/part_models/omni_wheel.SLDPRT
38.1 x 38.1 x 23.7 mm

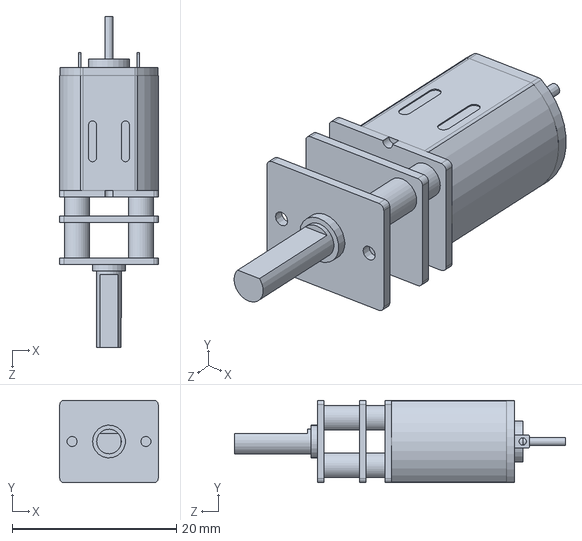
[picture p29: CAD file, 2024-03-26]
hardware/CAD/part_models/micro-metal-gearmotor-backshaft.SLDPRT
12.0 x 10.0 x 40.3 mm

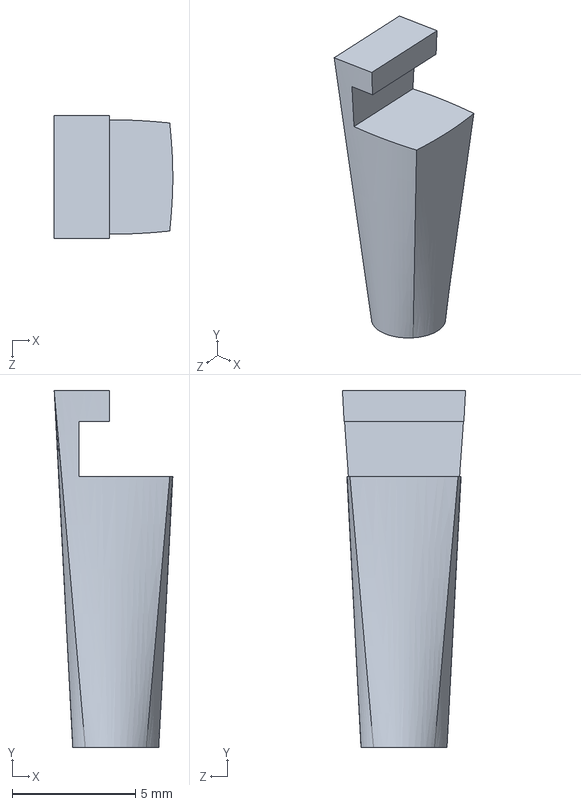
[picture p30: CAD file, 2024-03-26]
hardware/CAD/PCB_spacer.SLDPRT
4.82 x 14.5 x 5.00 mm

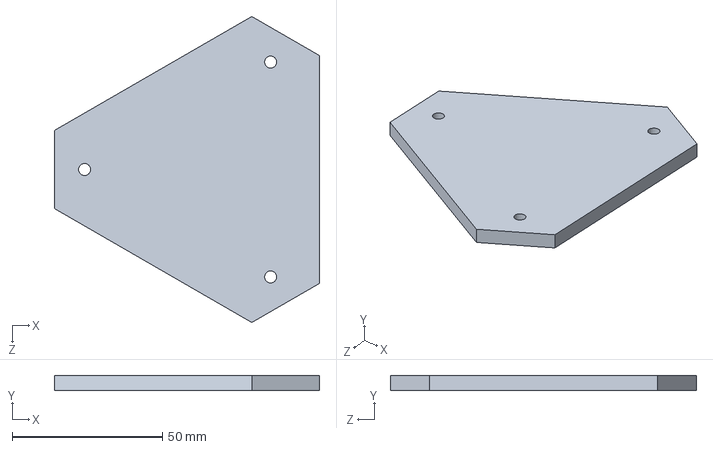
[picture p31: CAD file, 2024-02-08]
hardware/CAD/DR_lid_v4.SLDPRT
88.1 x 5.00 x 101.8 mm

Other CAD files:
hardware/CAD/DR_layer_spacer_v2.SLDPRT
hardware/CAD/part_models/layer_spacer.SLDPRT
hardware/CAD/part_models/DFRobot_Micro_Metal_Bracket.SLDPRT
hardware/CAD/DR_omni_coupler.SLDPRT
hardware/CAD/3d_print/DR_battery_housing_v5.STL
hardware/CAD/3d_print/DR_body_v5.STL
hardware/CAD/3d_print/PCB_spacer.STL
hardware/CAD/3d_print/lid_spacer.STL
hardware/CAD/DR_body_v4.SLDPRT
hardware/CAD/laser_cut/main_body_v4.DWG
hardware/CAD/part_models/PCB.SLDPRT
hardware/CAD/part_models/battery_housing_v3.SLDPRT
hardware/CAD/part_models/nexus 14184 38mm Omni Wheel v4.stl

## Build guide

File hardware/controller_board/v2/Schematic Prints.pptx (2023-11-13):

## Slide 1

Vin U2

C1

10uF

LD1086DT33TR

Vin Vout GND

VCC

1

Vcc_out

VCC

R1

100R

D1

D2

LED1

2

Battery

1
2

Vin

3

GND ².^2uF ⁰.⁰¹uF

C8 C9

Vin

4

A

10uF

C2

Header 2

1
2

R2

100R

D3

LED2

Battery

GND

VCC Motor2_A

Motor1_B

Motor1_A 15

Motor2_B

12

16

10

9

1

8

U3

VM AIN1 AIN2 BIN1 BIN2 nSLEEP nFAULT GND

VINT VCP AOUT1 AOUT2 AISEN BOUT1 BOUT2 BISEN

3

14

7

5

2

4

11 M1

M2

1
2

A

Voltage regulator

VCC

GND

LEDs

R3

100R

GND

Battery Port

Vin

GND

13

Dual H-Bridge Motor Driver

6

GND

Vin

1
2

B

C3

10uF

40

41

U1

(PCINT8/XCK0/T0) PB0 (PCINT9/CLKO/T1) PB1 (PCINT10/INT2/AIN0) PB2 (PCINT11/OC0A/AIN1) PB3 (PCINT12/OC0B/SS) PB4 (PCINT13/ICP3/MOSI) PB5 (PCINT14/OC3A/MISO) PB6 (PCINT15/OC3B/SCK) PB7

PA0 (ADC0/PCINT0) PA1 (ADC1/PCINT1) PA2 (ADC2/PCINT2) PA3 (ADC3/PCINT3) PA4 (ADC4/PCINT4) PA5 (ADC5/PCINT5) PA6 (ADC6/PCINT6) PA7 (ADC7/PCINT7)

37

36
35
34

Sens1

VCC

Motor3_A 16

Motor3_B

12

15

9

U4

VM AIN1 AIN2 BIN1 BIN2 nSLEEP nFAULT GND

VINT VCP AOUT1 AOUT2 AISEN BOUT1 BOUT2 BISEN

GND

14

11

2

4

C10 C11 2.2uF 0.01uF

M3

1
2

B

S0

Header 2

GND

1
2

Motor3_A 43

Motor3_B 44

MOSI 1

MISO

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
Sens2

GND

10

13

1

8

Dual H-Bridge Motor Driver

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
Motor1_B 13

Motor1_A 14

Motor2_B 15

Motor2_A 16

10

11

12

(PCINT24/RXD0/T3) PD0 (PCINT25/TXD0) PD1 (PCINT26/RXD1/INT0) PD2 (PCINT27/TXD1/INT1) PD3 (PCINT28/XCK1/OC1B) PD4 (PCINT29/OC1A) PD5 (PCINT30/OC2B/ICP) PD6 (OC2A/PCINT31) PD7

PC0 (SCL/PCINT16) PC1 (SDA/PCINT17) PC2 (TCK/PCINT18) PC3 (TMS/PCINT19) PC4 (TDO/PCINT20) PC5 (TDI/PCINT21) PC6 (TOSC1/PCINT22) PC7 (TOSC2/PCINT23)

20

21

22
23
24
25

26

LED1

LED2

Header 2

1
2

VCC

Motor Drivers

VCC

Sens2

Sensors

1 2
3 4
5 6

Sens1

VCC

MP

VCC

C

22pF

22pF

C6

XTAL
20Mhz

1

2

Y1

18

8

7

6

XTAL1 XTAL2

GND GND

RESET

AVCC

AREF

5

29

27

4

C4

100nf

Reset

L1 10uH

C7
100nf

Sensors Port

GND

Header 3X2H

GND

Vin

2

S1

SW-SPDT

1

3

GND

SCK

Reset

Header 4X2H

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
MOSI

MISO

Battery

C

GND

28

39

ATmega1284P-AU

GND

VCC

VCC

17

38

VCC

GND

RXD 2

TXD 3

VCC

1

4

U5

VDD
Dout Din DIO12 RESET! RSSI DIO11 RES DTR

DIO0 DIO1 DIO2 DIO3 RTS! DIO5 RES DIO9 CTS!

20

19

18

17

Multi-Purpose Port

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
Xbee

GND

DIO4

14

16

12

15

13

11

Title

D

uC unit

1

2

Xbee

3

Size A4

Date:

File:

\\..\Schematic_v2.SchDoc

10/10/2015

Number

Sheet of

Drawn By:

4

Revision

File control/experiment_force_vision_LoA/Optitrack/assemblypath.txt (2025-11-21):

C:\Users\user\MATLAB Drive\Research\experiment_force_vision_LoA\Optitrack\NatNetML.dll

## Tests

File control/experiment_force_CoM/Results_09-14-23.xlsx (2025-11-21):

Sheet: Sheet1
Payload | CoM Position | Actual Pos | Trial # | Final vector x | Final vector y
Circle | Up 50g | 0 16.32 | 1 | -119.84 | -120.57
 |  | 0 16.32 | 2 | -121.63 | -118.77
 |  | 0 16.32 | 3 | -126.94 | -113.07
 | Down 100g |  | 1 | -81.63 | -149.12
 |  |  | 2 | -68.42 | -155.62 | Down 100 weight placed at 61mm in negative y axis
 |  |  | 3 | -64.26 | -157.39
Polygon | Straight ahead |  | 1 |  |  | Ahead is 52mm in front of attachment point, 5 to the 'right' or 'up'
 |  |  | 2
 |  |  | 3
 | ? |  | 1 |  |  | Ahead is 44mm in front and 46mm 'left' or 'down'
 |  |  | 2
 |  |  | 3 |  |  | True blob CoM is 46mm in front of attach, 7mm left if attach is on the rhs like all measurements above
 |  |  |  |  |  | Can also find thru some program if I still have the blob shape
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

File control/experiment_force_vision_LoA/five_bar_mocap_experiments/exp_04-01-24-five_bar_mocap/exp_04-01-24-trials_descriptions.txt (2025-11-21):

u_r = [0;0;3500]

rotTrial = trial1:
P = 30
I = 2
D = 1.5

trial2:
P = 45
I = 2
D = 1.5

trial3:
P = 45
I = 2
D = 1

trial4:
P = 60
I = 2
D = 1.2

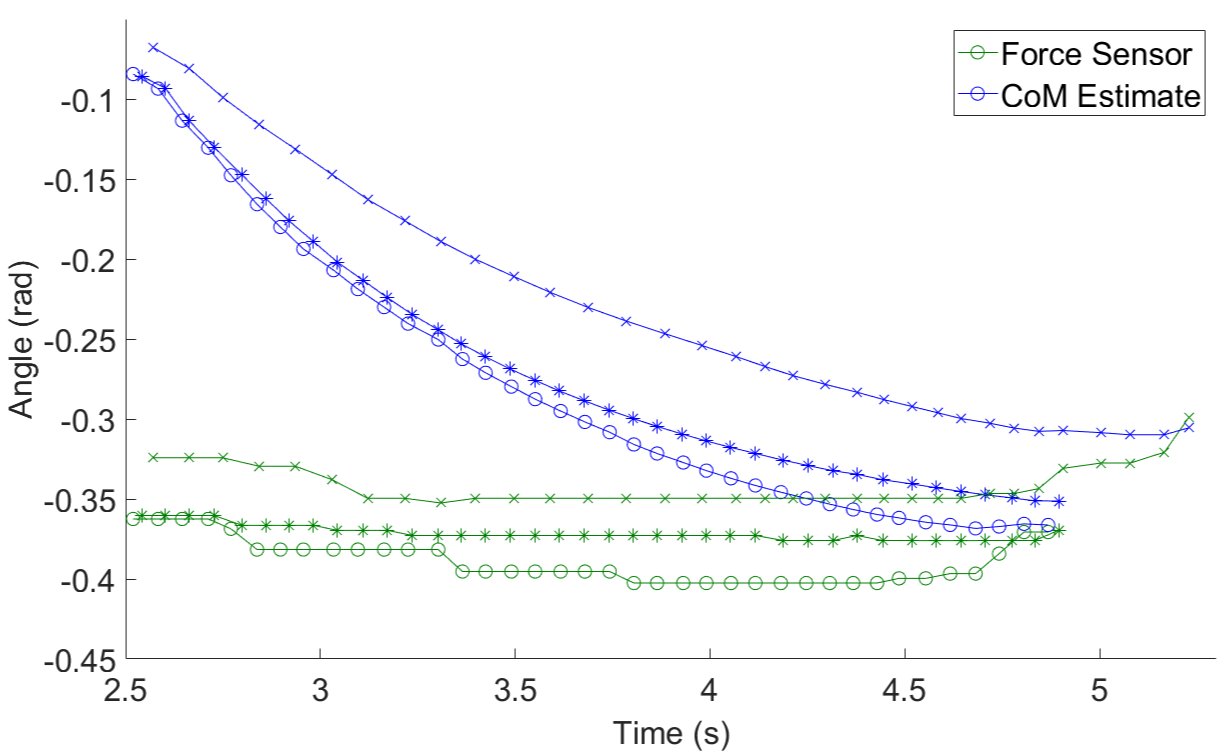
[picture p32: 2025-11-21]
control/experiment_force_CoM/Results_09-14-23/circ_response1.png

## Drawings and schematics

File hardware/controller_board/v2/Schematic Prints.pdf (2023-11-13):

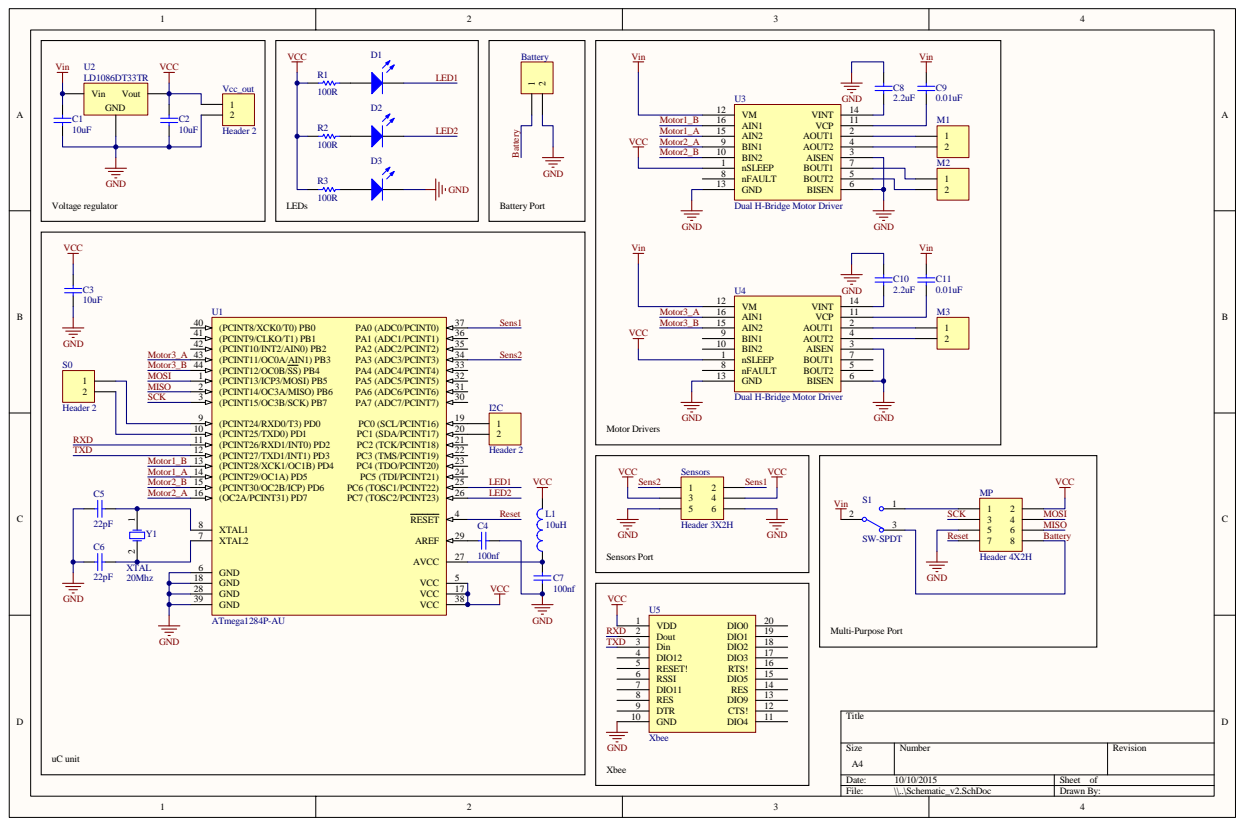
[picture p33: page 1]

Dual H-Bridge Motor Driver

Size A4 | Number | Revision

Date: 10/10/2015 | Sheet of
File: \\..\Schematic_v2.SchDoc | Drawn By:

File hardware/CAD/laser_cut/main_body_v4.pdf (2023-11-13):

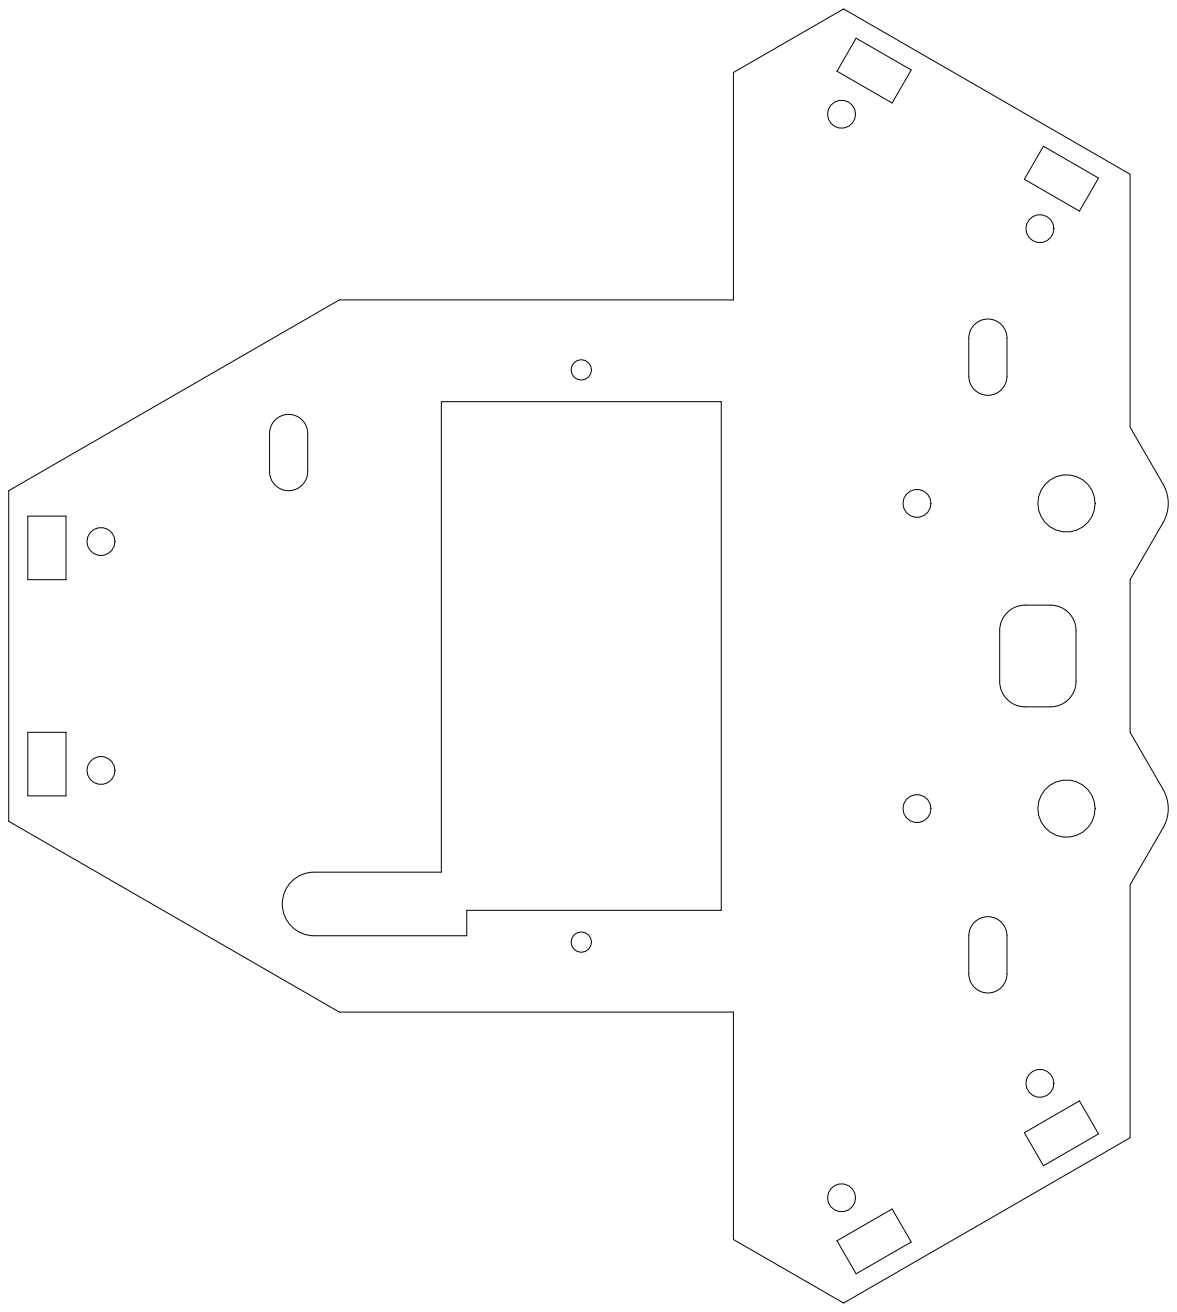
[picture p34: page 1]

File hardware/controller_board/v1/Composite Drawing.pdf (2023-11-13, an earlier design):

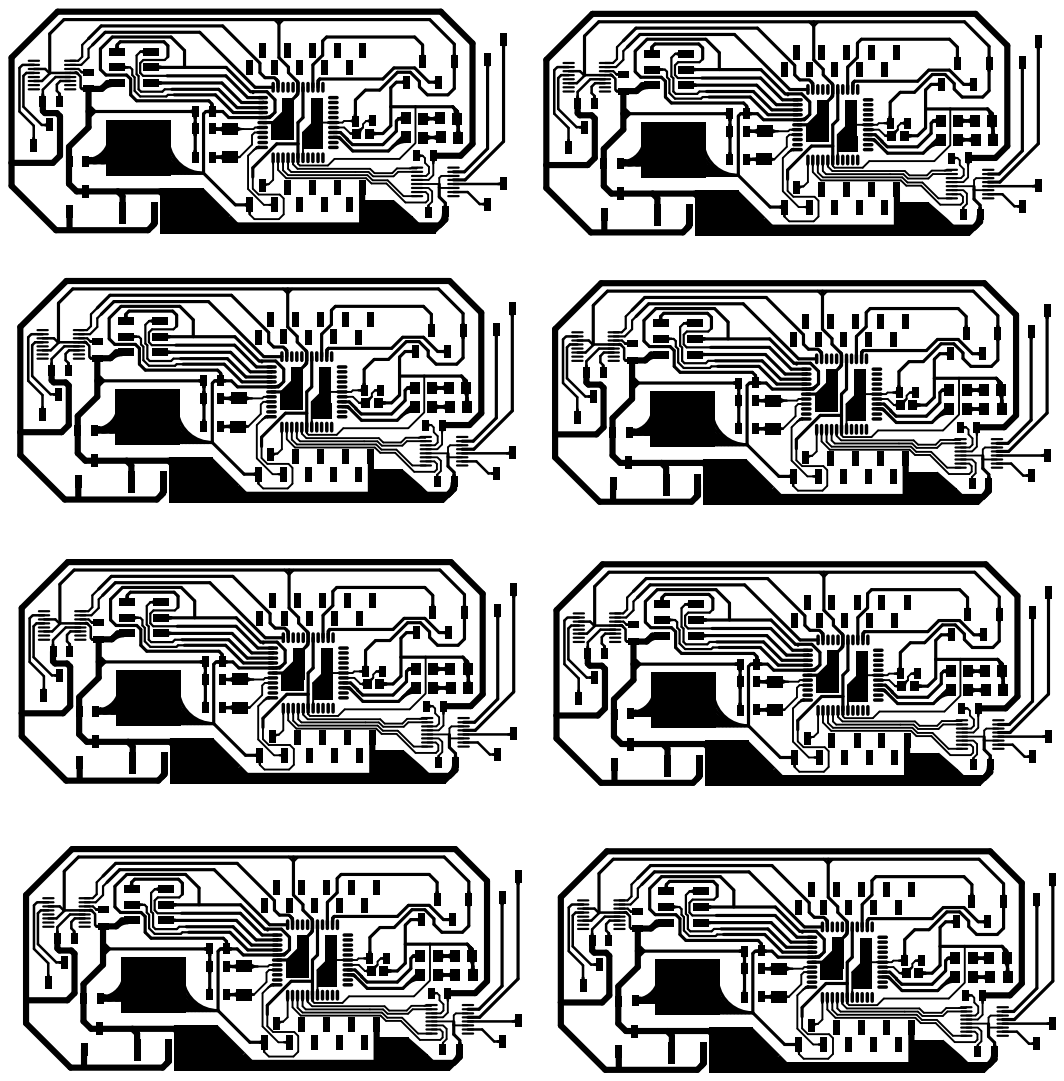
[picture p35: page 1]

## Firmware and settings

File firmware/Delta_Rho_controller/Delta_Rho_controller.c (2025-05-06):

//#include <\\research.wpi.edu\srl\Projects\Ant\Delta_Rho\Code\Libraries\DeltaRho.h>
#include "DeltaRho.h"
#include "config.h"

#include <math.h>
#include <time.h>
#include <util/twi.h>
#include "TWI_slave.h" 
#include "avr/sleep.h"

// ================= IMPORTANT: CHANGE RobotID =================
#define RobotID				10
// =============================================================
#define I2C_ADDR			0x08				// I2C Slave Address *** Square Pin 1 is SCL is Blue is pin15 on esp ***
#define POWER_MANAGEMENT_ENABLED				// Enable power management for TWI
#define STOP_UPPER			194					// UPPER acceptable payload rotation for att. corr.
#define STOP_LOWER			166					// LOWER acceptable payload rotation for att. corr.


// Legacy variables
volatile char start			= 0;
volatile int out[3], in[3];
volatile signed int xd[3], x[3], xO[3];

// Meta global vars
float daGlobal;								// Global variable for whatevs
int mode_switch				= 0;			// Mode Toggle (binary for now)
volatile int send_data[3]	= {0, 0, 0};	// For sending data wirelessly via XBee
	
// I2C & TWI setup
volatile int i2c_data		= 180;			// Global var to store latest received i2c data: 0x02 default value
unsigned char message_buf[TWI_BUFFER_SIZE];

// Robot Jacobian
float J_r[3][3]				= {{-0.9874, 0.0263, 0.0456}, {-7.8542, -0.0526, 0}, {-0.9874, 0.0263, -0.0456}}; // Default value
float J[3][3];

// Control input and input memory
float u_r[3]				= {0, 0, 0};	// Control Input
float u_r_mem[2]			= {0, 0};		// Memory for switching between CoM and attitude correction
		
// Primary Algorithm Variables
Vector2D neg_bound			= {1, 0.0001};	// Negative-most possibility for LoA (using right-hand-rule)
Vector2D pos_bound			= {-1, 0.0001};	// Positive-most possibility for LoA (using right-hand-rule)
float rot_mem				= 0;			// Payload rotation memory for stop condition
volatile int stop_counter	= 0;			// STOP counter for Line of Action estimate (when minimal rotation observed)
volatile int new_data_rec	= 0;			// Flag for I2C reception
int desired_vel				= 2650;			// Desired velocity of robot
int step					= 0;			// iterator
int att_switch				= 0;			// attitude correction switch
int STOP_SWITCH				= 0;			// STOP switch for ending experiment
float temp_mem				= 180;
	
// --- FORWARD DECLARATIONS ---
float			medianFilter(float arr[], int n);
Vector2D		rotateVector(Vector2D v_in, float angle);
unsigned char	TWI_Act_On_Failure_In_Last_Transmission(unsigned char TWIerrorMsg);


// ===========================================================================
// =======================     INTERRUPT     =================================
// ===========================================================================
ISR(USART1_RX_vect)
{
	//char i;
	char data, address;
	unsigned char requestedID, requestedCode;
	
	data = USART1_Receive();
	
	if(data == 0x55){ // Check for "Start" byte (85)
		
		address = USART1_Receive();
		requestedID = address & 0x0F;
		requestedCode = address & 0xf0;
		
		if( requestedID == RobotID || requestedID == 0x00 ){ // Check for correct robot ID
			PORTC &= ~BIT(redLED);
			switch ( requestedCode ){
				
				// NOTE: USART1_Receive() grabs each byte sequentially and 'consumes' it from the buffer. So the next time it 
				// is called, the next byte is retrieved ...
				
				case(0x00): // Desired position -> Read request (0)
					USART1_SerialSend(xd, 3);
				break;
				
				case(0x80): // Desired position -> Write request (128)
					USART1_SerialGet(xd, 3);
				break;
				
				case(0x10): // Current position -> Read request (16)
					USART1_SerialSend(x, 3);
				break;
				
				//case(0x90): // Current position -> Write request (144)
					//updateState(x,dx,&n_x,&t_x);
				//break;
				
				case(0x20): // Object position -> Read request (32)
					USART1_SerialSend(xO, 3);
				break;
				
				//case(0xA0): // Object position -> Write request (160)
					//updateState(xO,dxO,&n_o,&t_o);
				//break;
				
				case(0x30): // Send "out" data (48)
					USART1_SerialSend(out, 3);
				break;
				
				case(0xB0): // Get "in" data (176)
					USART1_SerialGet(in, 3);
				break;
				
				case(0x40): // Actuator values -> Read request (64)
				// USART1_SerialSend();
				break;
				
				case(0xC0): // Actuator values -> Write request (192)
					
					//thisVoltage[0] = USART1_Receive();
					//thisVoltage[1] = USART1_Receive();
					//thisVoltage[2] = USART1_Receive();
					//thisVoltage[3] = USART1_Receive();
					//thisVoltage[4] = USART1_Receive();
					//thisVoltage[5] = USART1_Receive();					
					//applyPulse();
					
					// Apply amplified (or non-amplified) voltages
					//FLCCW	= tempVoltage[0];
					//FLCW	= tempVoltage[1];
					//RCCW	= tempVoltage[2];
					//RCW		= tempVoltage[3];
					//FRCCW	= tempVoltage[4];
					//FRCW	= tempVoltage[5];
					
					FLCCW	= USART1_Receive();
					FLCW	= USART1_Receive();
					RCCW	= USART1_Receive();
					RCW		= USART1_Receive();
					FRCCW	= USART1_Receive();
					FRCW	= USART1_Receive();
				break;
				
				
				//////////////////////////////////////////////////////////////////////////
				// Hyland 11-16-22 - Adding sensor read request: SerialCommunication.m says 208, 224, 80, 96 are reserved...

				case(0x50): // Sensor Values -> Read request (80 in decimal)
				// SEND BASE ANGLES (degrees)
					//send_data[0] = (int) (raw_sensor_data.x * 100); // * 180/3.1415);
					//send_data[1] = (int) (raw_sensor_data.y * 100); // * 180/3.1415);
				// SEND EE POSITION (mm)
					//send_data[0] = (int) (EE[0] * 100);
					//send_data[1] = (int) (EE[1] * 100);
				// SEND u_r motor command
					//send_data[0] = (int) (u_r[0] * 100);
					//send_data[1] = (int) (u_r[1] * 100);
					//send_data[2] = (int) (u_r[2] * 100);
								
				// SEND I2C DATA from esp-cam
					send_data[0] = (int) i2c_data;
					send_data[1] = (int) new_data_rec;
				// SEND WHATEVER GLOBAL DATA YOU WANT YO
					//send_data[0] = daGlobal;
					//send_data[1] = daGlobal;
					
					
					USART1_SerialSend(send_data, 3);					
				break;
				
				
				case(0xD0): // Switch actuation mode -> Write request (208 in decimal)
					mode_switch	= !mode_switch; // Toggle from zero-force mode to driving mode.
				break;
				
				case(0xE0) : // Switch actuation to mode 3 -> Write request (224 in decimal)
					mode_switch = 2; // Switch to mode 3 (temporary, need to instead send a serial packet with the mode num)
				break;
				//////////////////////////////////////////////////////////////////////////
				
				case(0x70): // Reset (112)
					start = 1;
				break;
				
				case(0xF0): // Stop/Sleep (240)
				
				break;
	
			} // End of: switch
		} // End of: if ID match	
	} // End of: if start
	PORTC |= BIT(redLED);
}


// ===========================================================================
// =====================     I2C & MOTOR COMMS     ===========================
// ===========================================================================

//		I2C Receive from Master
//========================================================================
void runTWI (void){
	
	if ( ! TWI_Transceiver_Busy() ) {			// Check if transceiver has completed operation
		if ( TWI_statusReg.lastTransOK ) {		// Check if last operation was success
			if ( TWI_statusReg.RxDataInBuf ) {	// Check if last operation was reception
				TWI_Get_Data_From_Transceiver(message_buf, 4);
				message_buf[4] = '\0';			// Null-terminate the string
				i2c_data = atoi((char*)message_buf);
				new_data_rec = 1;			// Set i2c reception flag to TRUE
			}
			
			if ( ! TWI_Transceiver_Busy() ) {	// Check if transceiver already started
				TWI_Start_Transceiver();		// If not, restart it to prepare for new receptions
			}
		}
		else {									// Ends up here if last operation unsuccessful
			TWI_Act_On_Failure_In_Last_Transmission( TWI_Get_State_Info() );
		}
	}
}

//		Send current signal to motors ************* TODO FIX THIS *************
//========================================================================
void sendMotor(void){
	// Send u_r after converting to motor currents
	unsigned char u[3][2];
	float f[3] = {0,0,0};
	signed int temp;
	
	// Update Jacobian given new EE position (actual attachment to payload)
	calculateJacobian(EE[0], EE[1], J);
	
	// Perform the matrix multiplication J_r * u_r
	for (int i = 0; i < 3; i++) {
		for (int j = 0; j < 3; j++) {
			f[i] += J_r[i][j] * u_r[j]; // 09-10-24 TEMP CHANGING TO J_r for default value
		}
	}
	
	// 09-10-24 REAR WHEEL SEEMS WEAK. AMPLIFYING A LITTLE BIT TO GET STRAIGHT 
	// LINE DIAGONAL MOTION
	f[1] *= 1.75;
	
	// Assign to wheel array
	for (int i = 0; i < 3; i++){
		temp = (int)roundf(f[i]);
		if(temp > 255){
			temp = 255;
		}
		else if(temp < -255){
			temp = -255;
		}
		if(temp >= 0){
			u[i][0] = 0;
			u[i][1] = abs(temp);
		}
		else{
			u[i][0] = abs(temp);
			u[i][1] = 0;
		}
	}
	
	// Apply stiction pulse if needed
	thisVoltage[0] = u[0][0];
	thisVoltage[1] = u[0][1];
	thisVoltage[2] = u[1][0];
	thisVoltage[3] = u[1][1];
	thisVoltage[4] = u[2][0];
	thisVoltage[5] = u[2][1];
	//applyPulse();
	
	//// Front Left
	//FLCCW = tempVoltage[0];
	//FLCW = tempVoltage[1];
	//// Rear
	//RCCW = tempVoltage[2];
	//RCW = tempVoltage[3];
	////Front Right
	//FRCCW = tempVoltage[4];
	//FRCW = tempVoltage[5];
	
	
	// Checking to see if this is messing me up
	
	// Front Left
	FLCCW = u[0][0];
	FLCW = u[0][1];
	// Rear
	RCCW = u[1][0];
	RCW = u[1][1];
	//Front Right
	FRCCW = u[2][0];
	FRCW = u[2][1];
}


// ===========================================================================
// ======================     ALGORITHM FUNCTIONS     ========================
// ===========================================================================

//		Cancel out force measured by sensor
//========================================================================
void nullSpaceControl (void) {
	
	// u_r[0] is X motion (Forw+/Backw-)
	// u_r[1] is Y motion (Right+/Left-)
	// u_r[2] is Z motion (CCW+/CW-)
		
	float gainX; // gain in ROBOT's X direction
	float gainY; // gain in ROBOT's Y direction
	
	gainY = 20;
	gainX = gainY;
	// Sensor displacement 'away' from robot has dampened so increase the 'fwd/back' gain
	if (EE[1] > 3) {
		gainX += 10;
	}

	// Sensor 'x' is robot 'y' and vice-versa
	u_r[0] = EE[1]*gainX;
	u_r[1] = EE[0]*gainY;
	u_r[2] = 0;
	
	sendMotor();
}


//		Get random angle for perturbation of LoA Search
//========================================================================
void perturbation (void) {
	Vector2D temp_u = {u_r[1], u_r[2]};
	Vector2D rot_u;
	
	float perturbation_angle = ((float)rand() / (float)RAND_MAX - 0.5) * M_PI / 12.0;  // +/- 15 degrees
	
	rot_u = rotateVector(temp_u, perturbation_angle);
	u_r[1] = rot_u.x;
	u_r[2] = rot_u.y;
}


//		Correct the attitude of the robot using force sensor
//========================================================================
void correctAttitude (PIDController *pid_att) {
	// u_r = [Z X Y] (Clockwise, Right, Forward)
	
	// ----- PID Controller -----
	float error			= pid_att->setPoint - i2c_data;
	pid_att->integral	+= error;
	float derivative	= (error - pid_att->prevError);
	float output		= pid_att->Kp  * error   +   pid_att->Ki  *  pid_att->integral   +   pid_att->Kd  * derivative;
	pid_att->prevError	= error;

	// ==== Assign to Control Input Array ====
	u_r[0]				= output;	// Assign z-axis motor command
}

//		LoA Search - Binary Search Algorithm
//========================================================================
void loaSearch (void) {
	// u_r = [Z X Y] (Clockwise, Right, Forward)
		
	// Determine payload rotation sense with force feedback
	Vector2D f_s			= {-EE[0],		-EE[1]};	 // Force sensor 'direction' - opposite of reading (flip EE vector)
	Vector2D f_r			= {u_r_mem[0],	u_r_mem[1]}; // Robot heading from input - TODO update with IMU / mocap / encoders
	
	// Get angle of force and heading vectors w.r.t. +x axis
	float angle_f_r			= atan2f(f_r.y, f_r.x);
	float angle_f_s			= atan2f(f_s.y, f_s.x);
	// Get rotation sense based on angle between motion and force feedback (-1 or 1 using RHR)
	float rot_amt			= (angle_f_s - 0.01) - angle_f_r; // -.02 TEMPORARY: SUBTRACT A SMALL ERROR CAUSE OF THE SENSOR BIAS TOWARDS THE RIGHT
	float rot_sense			= rot_amt / abs(rot_amt);
	
	//IDEA: CREATE AN ARRAY OR HISTORY OF 'SENSE' OR EVEN JUST ADD HISTORY (-1 + 1 + -1 + -1)=NEG SENSE
	
	
	// ALGORITHM EDGE CASE CATCHING
	if (f_s.y < -1.5)			// (mm) Retain heading when force is 'away' from robot (pulling payload)
		return;
	if (sqrt(pow(f_s.x, 2) + pow(f_s.y, 2)) < 4) // Catch when force is minimal (for testing mainly)
		return;
	if (abs(rot_amt) < 0.03)	// 0.052=3deg (0.09 = 5deg) Catch when angle b/w motion & force minimal. Continue pushing (Sensor uncertainty)
		return;
	step++;						// Increment step counter 
	if (step % 5 != 0)			// Step counter to check stop condition every time step, but only update bounds every nth step
		return;
	
	// Set new bounds based on rotation sense (make it a unit vector)
	float u_r_mag			= sqrt(pow(u_r_mem[0], 2) + pow(u_r_mem[1], 2));
	if (rot_sense >= 0) {
		neg_bound.x			= u_r_mem[0] / u_r_mag;
		neg_bound.y			= u_r_mem[1] / u_r_mag;
	}
	else {
		pos_bound.x			= u_r_mem[0] / u_r_mag;
		pos_bound.y			= u_r_mem[1] / u_r_mag;
	}
	
	// Get new push direction by summing bounds (same as bisecting)
	float output_x			= pos_bound.x + neg_bound.x;
	float output_y			= pos_bound.y + neg_bound.y;
	// Make unit vector and apply desired velocity simultaneously
	float output_mag		= sqrt(pow(output_x, 2) + pow(output_y, 2));
	output_x				*= (desired_vel/output_mag);
	output_y				*= (desired_vel/output_mag);
	
	// ==== Assign to Control Input Array ====
	u_r[1]					= output_x;
	u_r[2]					= output_y;
	
	// == TEMP - Add a perturbation to u_r ==
	perturbation();
	
	// Assign motion memory to new motion command
	u_r_mem[0]			= u_r[1];
	u_r_mem[1]			= u_r[2];
}

//================================================================================================
//************************************       MAIN       ******************************************
//================================================================================================
int main(void){
	mC_init();					// Initialize micro controller

	// Initialize TWI module for slave operation. Include address and/or enable General Call
	TWI_Slave_Initialise((unsigned char)((0x08<<TWI_ADR_BITS) | (TRUE<<TWI_GEN_BIT) )); // TRUE
	sei();						// Enable global interrupts
	TWI_Start_Transceiver();	// Enable reception of first command from master
		
	// Start timer3 (unused?)
	TCNT3H = 0;
	TCNT3L = 0;
	TIMSK3 |= (1<<TOIE3);		// Enable Timer3 overflow interrupt - ChatGPT advised
	PORTC |= BIT(redLED);		// Turn ON redLED
	PORTC &= ~BIT(blueLED);		// Turn OFF blueLED
	
	getHome();					// Get force sensor home position and assign to 'home'
	srand(time(NULL));			// Set the seed for rng
	int iii = 0;				// iterator
			
	// ===== PID INITIALIZATIONS (Kp, Ki, Kd, setPoint) ====
	PIDController pid_att; // pid_com, pid_att;
	//PID_Init(&pid_com, 1, 0, 0.08, 0); // 0.8, 0, 0.08 for 6 // 1, 0, 0 works OK but maybe too aggressive (it's immediately changing direction towards force feedback)
	PID_Init(&pid_att, 1.25, 0.05, 0.2, 180); // 1.25, 0.05, 0.2 is critically damped for robot 5


	// ========== PRIMARY LOOP ==========
	while(start == 0){
		runTWI();				// Run all i2c communications (receive camera info)
		sensorKinematics();		// Force feedback, assigned to EE var
		
		// Defaults to case 0. Change modes via MATLAB
		switch (mode_switch) {
			// ---------------------------------------------------------------------------------------------------
			case 0:
			
			// ============================================================
				// When not in on-board mode, send initial 'stop' command
				//if (iii != 0){
					//u_r[0] = u_r[1] = u_r[2] = 0;
					//sendMotor();
				//}
				//iii = 0;
			// ============================================================
			
				PORTC ^= BIT(blueLED);				// Toggle blueLED
				_delay_ms(100);						// Rapid heartbeat
				break;

			case 1:
				correctAttitude(&pid_att);
				//u_r[1] = 2900 * -0.2;
				//u_r[2] = 2900 * 0.98;
				sendMotor();
				break;

			case 2:
				while (iii <= 800){
					iii ++;
					u_r[2]			= u_r_mem[1] = desired_vel;	// Induce motion and set initial 'memory' as 'forward'
					u_r_mem[0]		= 0;
					sendMotor();
					stop_counter	= 0;			// Reset stop counter for multiple trials w/o restarting robot
					neg_bound.x		= 1;
					pos_bound.x		= -1;
					neg_bound.y		= pos_bound.y = 0.0001;		// Reset bounds
					rot_mem			= 0;
					STOP_SWITCH		= 0;			// Reset global stop
					att_switch		= 0;
					temp_mem		= 180;
					step			= 0;
				}


				//  === Want to do EITHER LoA search OR correct attitude ===
				
				// If wheel about to collide, activate attitude control
				if (i2c_data <= STOP_LOWER || i2c_data >= STOP_UPPER) {
					att_switch = 1; // Turn ON attitude control, stop LoA search
					u_r[1] = 0;
					u_r[2] = 0;
				}
				if (i2c_data >= 170  && i2c_data <= 190){ // 179 and 181 If attitude control is done turn OFF attitude control switch
					att_switch = 0;
					u_r[0] = 0;
					u_r[1] = u_r_mem[0]; // Resume prior motion
					u_r[2] = u_r_mem[1];
				}
				
				// Attitude control switching
				if (att_switch) {
					correctAttitude(&pid_att);
					// STOP CONDITION RESET
					stop_counter = 0;
				}
				else {
					loaSearch();
					correctAttitude(&pid_att);
					// STOP CONDITION CHECK
					if (abs(i2c_data - rot_mem) < 0.052) //10 deg // 0.09=5 degrees  // .052 = 3 degrees // Increment if payload vs robot orientation small rate of change
					stop_counter ++;
				}
				
				rot_mem = i2c_data;
				
				// END EXPERIMENT
				if (stop_counter >= 40 || STOP_SWITCH == 1){			// Check for STOP condition
					STOP_SWITCH	= 1;				// Enable global stop
					EE[0] = EE[1] = 0.69;			// SET EE to 'stop value' so MATLAB can change mode. Easier for data collection.
					u_r[0] = u_r[1] = u_r[2] = 0;	// And stop robot motion (untested)
				}
				
				sendMotor();						// Send all motor commands
				
				PORTC ^= BIT(blueLED);				// Toggle blueLED
				_delay_ms(100);						// Rapid heartbeat
				
				break;
		}
	}
	
	//PORTC |= BIT(blueLED);		// Turn ON blueLED
	TCCR3B = (1<<CS32) | (0<<CS31) | (1<<CS30);
		
	return 0;
}

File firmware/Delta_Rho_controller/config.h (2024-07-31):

// Configuration and helper fns for Robot Controllers

#define NUM_SAMPLES			5	 // Number of sensor samples for mean filtering
#define THRESHOLD_VOLTAGE	80	 // Below this voltage, motors may not move
#define FORCE_DEADZONE		4	 // Force sensor deadzone (small issue with force sensor)

volatile unsigned char n_x, n_o; // = 0;
volatile uint32_t overflowCount = 0;

// Add 'pulse' to overcome stiction
int thisVoltage[6], tempVoltage[6], lastVoltage[6]; // = {0, 0, 0, 0, 0, 0};

// 2D Vector structure
typedef struct {
	float x;
	float y;
} Vector2D;

// PID structure
typedef struct {
	double Kp; // Proportional gain
	double Ki; // Integral gain
	double Kd; // Derivative gain

	double integral;
	double prevError;
	double setPoint; // Desired value of the process variable
} PIDController;


// Force Sensor
float Links[5] = {25.0, 25.0, 40.0, 40.0, 22.84};
float EE[2] = {0, 0};
Vector2D home = {0, 0};							// Force sensor home EE position
Vector2D raw_sensor_data = {729.211, 418.9086}; // Hard-coded voltages representing 120 and 60 degs


//		ISR for Timer3
//========================================================================
ISR(TIMER3_COMPA_vect) {
	n_x ++; // Increment on every Compare Match interrupt
	n_o ++;
	
	overflowCount ++; // Increment overflow count when timer reaches max value
}

// ===========================================================================
// ========================     MOTOR FUNCTIONS     ==========================
// ===========================================================================

//		Stiction overcome function
//========================================================================
void applyPulse(void){
	// Takes 'thisVoltage' and compares it to a threshold AND to the 'lastVoltage' to determine
	// if a pulse is needed to kickstart the motor motion.
	
	for (int i=0; i<6; i++){
		if (thisVoltage[i] != 0) {
			if (thisVoltage[i] < THRESHOLD_VOLTAGE && thisVoltage[i] != lastVoltage[i]) {
				tempVoltage[i] = 255;   // Apply the pulse voltage (255 is max)
			}
			else {
				tempVoltage[i] = thisVoltage[i];
			}
		}
		else {
			tempVoltage[i] = thisVoltage[i];
		}
	}
	
	// Set the previous voltage to the current voltage
	lastVoltage[0] = thisVoltage[0];
	lastVoltage[1] = thisVoltage[1];
	lastVoltage[2] = thisVoltage[2];
	lastVoltage[3] = thisVoltage[3];
	lastVoltage[4] = thisVoltage[4];
	lastVoltage[5] = thisVoltage[5];
	
}

//		Reconstruct Robot Jacobian Based on Sensor
//========================================================================
void calculateJacobian(float sx, float sy, float J[3][3]) {
	// Hardware values
	float beta[3] = {-1.0472, 1.0472, 3.1415};
	float w = 107.822;
	float h1 = 31.1235;
	float h2 = 62.25;
	float wheel_r = 19;
	
	// sx,sy inputs are actually EE pos in {sens} frame (9.7, 50.1) by default
	
	// Add to EE pos the distance to the robot frame {b}.
	sy += (36.88 + 10); // 36.88 is {sens} to {b}, 2nd num is empirical correction factor
	
	// C is the distance from center of rotation {EE for now} to wheel (FR, FL, R)
	sx = 9.7;
	sy = 50.1 + 36.88 + 10;
	double C[3][2] = {{(w/2 - sx), h1-sy}, {(-w/2 - sx), h1-sy}, {-sx, (-h2-sy)}};
	
	float J_temp[3][3];
	// Construct the Jacobian
	for (int i = 0; i < 3; i++) {
		J_temp[i][0] = (C[i][0]*sin(beta[i]) - C[i][1]*cos(beta[i])) / wheel_r;
		J_temp[i][1] = cos(beta[i]) / wheel_r;
		J_temp[i][2] = sin(beta[i]) / wheel_r;
	}
	
	// Swap the order for correct wheel assignment in sendMotor()
	J[0][0] = J_temp[1][0];
	J[0][1] = J_temp[1][1];
	J[0][2] = J_temp[1][2];
	
	J[1][0] = J_temp[2][0];
	J[1][1] = J_temp[2][1];
	J[1][2] = J_temp[2][2];
	
	J[2][0] = J_temp[0][0];
	J[2][1] = J_temp[0][1];
	J[2][2] = J_temp[0][2];
}

// ===========================================================================
// =======================     HELPER FUNCTIONS     ==========================
// ===========================================================================

//		I2C Error Handling Function
//========================================================================
unsigned char TWI_Act_On_Failure_In_Last_Transmission (unsigned char TWIerrorMsg)
{
	// A failure has occurred, use TWIerrorMsg to determine the nature of the failure
	// and take appropriate actions.
	// Se header file for a list of possible failures messages.
	
	// This very simple example puts the error code on PORTB and restarts the transceiver with
	// all the same data in the transmission buffers.
	//receivedI2C = TWIerrorMsg;
	TWI_Start_Transceiver();
	
	return TWIerrorMsg;
}

//		PID initialization function
//========================================================================
void PID_Init(PIDController* pid, double Kp, double Ki, double Kd, double setPoint) {
	pid->Kp = Kp;
	pid->Ki = Ki;
	pid->Kd = Kd;
	pid->integral = 0.0;
	pid->prevError = 0.0;
	pid->setPoint = setPoint;
}
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

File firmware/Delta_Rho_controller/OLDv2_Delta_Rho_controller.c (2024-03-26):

#include <\\research.wpi.edu\srl\Projects\Ant\Delta_Rho\Code\Libraries\DeltaRho.h>

#include <math.h>
#include <time.h>
//#include <DeltaRho.h>

// REMEMBER TO CHANGE ROBOTid FOR EACH ROBOT
#define RobotID 3
//#define Kp 10


volatile signed int xd[3] = {0,0,0};
volatile signed int x[3] = {0,0,0};
volatile signed int xO[3] = {0,0,0};
	
volatile signed int dx[3] = {0,0,0};
volatile signed int dxO[3] = {0,0,0};
		
volatile float F_R[3] = {0,0,0};

volatile int out[3] = {0,0,0};
volatile int in[3] = {0,0,0};

volatile char start = 0;


// Hyland - FORCE SENSOR Variables
float sensor_data[2] = {0.0, 0.0};
const float Links[5] = {25.0, 25.0, 40.0, 40.0, 22.84};
float p1[2] = {0, 0};
float p2[2] = {22.84, 0};
float p3[2] = {0, 0};
float p4[2] = {0, 0};
	
float EE[3] = {0, 0};
float home[2] = {0, 0};

volatile int send_EE[3] = {0, 0, 0};
volatile int send_sensor[3] = {0, 0, 0};
	
// Hyland - Mode Toggle (binary for now)
int mode_switch = 0;
float u_r[3] = {0, 0, 0};

// Hyland - Jacobian
float J_r[3][3] = {{0.8192, 0.5736, -0.1621}, {0.0, -1.0, -1.36}, {-0.8192, 0.5736, -0.1621}};

// Hyland - State estimate
float curr_X[3] = {0, 0, 0};
volatile int send_X[3] = {0, 0, 0};
	
// Hyland - Fixing Timer function
double t = 0;
double t_run = 0;
volatile uint32_t overflowCount = 0;

volatile unsigned int t_x = 0;
volatile unsigned int t_o = 0;
volatile unsigned char n_x = 0;
volatile unsigned char n_o = 0;

// Hyland - PID structure
typedef struct {
	double Kp; // Proportional gain
	double Ki; // Integral gain
	double Kd; // Derivative gain

	double integral;
	double prevError;
	double setPoint; // Desired value of the process variable
} PIDController;

// Hyland - Vec structure
// Define a struct for a 2D vector
typedef struct {
	double x;
	double y;
} Vector2D;


ISR(USART1_RX_vect)
{
	//char i;
	char data, address;
	unsigned char requestedID, requestedCode;
	
	data = USART1_Receive();
	
	if(data == 0x55){ // "Start" byte (85)
		
		address = USART1_Receive();
		requestedID = address & 0x0F;
		requestedCode = address & 0xf0;
		
		if( requestedID == RobotID || requestedID == 0x00 ){
			PORTC &= ~BIT(redLED);
			switch ( requestedCode ){
				
				case(0x00): // Desired position -> Read request (0)
					USART1_SerialSend(xd, 3);
				break;
				
				case(0x80): // Desired position -> Write request (128)
					USART1_SerialGet(xd, 3);
				break;
				
				case(0x10): // Current position -> Read request (16)
					USART1_SerialSend(x, 3);
				break;
				
				//case(0x90): // Current position -> Write request (144)
					//updateState(x,dx,&n_x,&t_x);
				//break;
				
				case(0x20): // Object position -> Read request (32)
					USART1_SerialSend(xO, 3);
				break;
				
				//case(0xA0): // Object position -> Write request (160)
					//updateState(xO,dxO,&n_o,&t_o);
				//break;
				
				case(0x30): // Send "out" data (48)
					USART1_SerialSend(out, 3);
				break;
				
				case(0xB0): // Get "in" data (176)
					USART1_SerialGet(in, 3);
				break;
				
				case(0x40): // Actuator values -> Read request (64)
				// USART1_SerialSend();
				break;
				
				case(0xC0): // Actuator values -> Write request (192)
					FLCCW = USART1_Receive();
					FLCW = USART1_Receive();
					RCCW = USART1_Receive();
					RCW = USART1_Receive();
					FRCCW = USART1_Receive();
					FRCW = USART1_Receive();
				break;
				
				
				//////////////////////////////////////////////////////////////////////////
				// Hyland 11-16-22 - Adding sensor read request: SerialCommunication.m says 208, 224, 80, 96 are reserved...

				case(0x50): // Sensor Values -> Read request (80 in decimal)
				
					// SEND BASE ANGLES (degrees)
					//send_sensor[0] = (int) (sensor_data[0] * 180/3.1415);
					//send_sensor[1] = (int) (sensor_data[1] * 180/3.1415);
					//USART1_SerialSend(send_sensor, 3);
					
					// SEND EE POSITION (mm)
					//send_EE[0] = (int) (u_r[0]); // * 100);
					//send_EE[1] = (int) (u_r[1]); // * 100);
					//USART1_SerialSend(send_EE, 3);
					
					// SEND STATE ESTIMATE (mm)
					send_X[0] = (int) (curr_X[0]); // * 100000);
					send_X[1] = (int) (curr_X[1]); // * 100000);
					send_X[2] = (int) (curr_X[2]); // * 100000);
					USART1_SerialSend(send_X, 3);
				break;
				
				
				case(0xD0): // Switch actuation mode -> Write request (208 in decimal)
					mode_switch	= !mode_switch; // Toggle from zero-force mode to driving mode.
				
				break;
				//////////////////////////////////////////////////////////////////////////
				
				case(0x70): // Reset (112)
					start = 1;
				break;
				
				case(0xF0): // Stop/Sleep (240)
				
				break;
	
			}	// End of: switch
		} // End of: if ID match	
	}	// End of: if start
	PORTC |= BIT(redLED);
}

ISR(TIMER3_COMPA_vect) {
	n_x ++; // Increment on every Compare Match interrupt
	n_o ++;
	
	overflowCount ++; // Increment overflow count when timer reaches max value
}

// PID initialization function
void PID_Init(PIDController* pid, double Kp, double Ki, double Kd, double setPoint) {
	pid->Kp = Kp;
	pid->Ki = Ki;
	pid->Kd = Kd;
	pid->integral = 0.0;
	pid->prevError = 0.0;
	pid->setPoint = setPoint;
}

float calculateTime(unsigned char *n, unsigned int *timerValue){
	
	float time = 0;
	unsigned int CurrentTimer;
	
	// Get current timer time from MCU
	CurrentTimer = TCNT3;
	
	// Get change in time from previous timerValue
	time =  *n*(OCR3A + 1) + CurrentTimer - *timerValue;
	
	// Reset n and set timerValue to currentTimer
	*n = 0;
	*timerValue = CurrentTimer;
	
	// Apply timer scaling factor (clocks per sec)
	time = time * 0.0001024;
	
	return time;
}

double getDt(){
	// Get elapsed MCU ticks. Overflow # is 65536 -> count nOverflows. TCNT3 is current timer
	uint32_t elapsedTicks = (overflowCount * 65536) + TCNT3;
	// Divide numTicks by CPU Freq 2 MHz
	double current_t = (elapsedTicks / (double) 20000000);
	// Get difference from previous call
	double diff_t = current_t - t_run;
	// Update total run time
	t_run = current_t;
	
	return diff_t;
	
}

void updateState(signed int* X, signed int *dX, unsigned char* n, unsigned int* timerValue){
	
	char i;
	float time;
	signed int X_old;
	unsigned char regl, regh;
	
	time = calculateTime(n, timerValue);
	
	for(i=0;i<3;i++){
		X_old = X[i];
		
		regl = USART1_Receive();
		regh = USART1_Receive();
		((signed int*)X)[i] = ((regh << 8) | regl);
		
		((signed int*)dX)[i] = (((int *)X[i]) - X_old);
	}
	
}
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

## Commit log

2023-11-13 Added code, CAD, and media
    [260mAh_battery.SLDPRT, 9271K93_Torsion Spring.SLDPRT, 9271K94_Torsion Spring.SLDPRT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]
2023-11-13 Cleaned up files, reduced file sizes
    [Digi-key order.xls, MyPcbLib.PcbLib, MySchLib.SchLib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]
2023-11-13 Removed unnecessary files
    [9271K93_Torsion Spring.SLDPRT, 9271K94_Torsion Spring.SLDPRT, Assem_large_spring.SLDASM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]
2024-01-09 Added on-board sensing
2024-01-10 Make robot respond to sensor input.
2024-02-08 Updated Firmware, CAD from GDrive
    [DR_battery_housing_v4.SLDPRT, DR_body_v4.SLDPRT, DR_lid_spacer_v4.SLDPRT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]
2024-03-06 Updated mode switch to accept remote input
2024-03-26 Cleaned up code
    [260mAh_battery.SLDPRT, DFRobot_Micro_Metal_Bracket.SLDPRT, DR_battery_housing_v5.SLDPRT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]
2024-04-12 Updated robot 5, old robot board died
2024-06-06 Lots of updates. Fixed force sensor code.
    [Delta_Rho_controller.c, OLD_Delta_Rho_controller.c, OLDv2_Delta_Rho_controller.c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]
2024-07-12 Updated Cad
    [5bar.SLDPRT, DR_battery_housing_v4.SLDPRT, DR_body_v5.SLDPRT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]
2024-07-16 Started implementing i2c
2024-07-19 Still trying to make i2c work.
    Now going to try i2c library made by avr
2024-07-22 Still trying for i2c
2024-07-22 Robot now receives i2c!
2024-07-23 I2C Works! Negative integers still do not work.
    [Delta_Rho_controller.c]
2024-07-25 Fixed issue with i2c value stored as uint8
    [Delta_Rho_controller.c]
2024-07-26 Updated CAD Naming
    [DR_layer_spacer_v2.SLDPRT, DR_lid_spacer_v4.SLDPRT, assem_full_robot_v4.SLDASM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]
2024-07-29 On-board camera attitude control implemented.
2024-07-30 Still fixing attitude control ...
    [Delta_Rho_controller.c]
2024-08-01 Got CoM + Attitude tuned nicely.
    Could still use a little fixing. Robot seems to over-correct attitude and 'forget' previous push direction.
    [Delta_Rho_controller.c]
2024-11-06 Changed mode switch function in main to case.
2024-11-06 Updated switch case and added SerialComms entry
2025-02-26 Added Matlab Control Scripts
    [Full_Robot_Costs.xlsx]
2025-11-21 Added all MATLAB control files
    [+45-deg-data_2023_09_03.csv, +45-deg-data_2023_09_11.csv, -45-deg-data_2023_09_03.csv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]
